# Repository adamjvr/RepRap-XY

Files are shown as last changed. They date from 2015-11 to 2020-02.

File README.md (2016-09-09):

# RepRap-XY-Iteration-2
## Open Source CoreXY RepRap 3D Printer
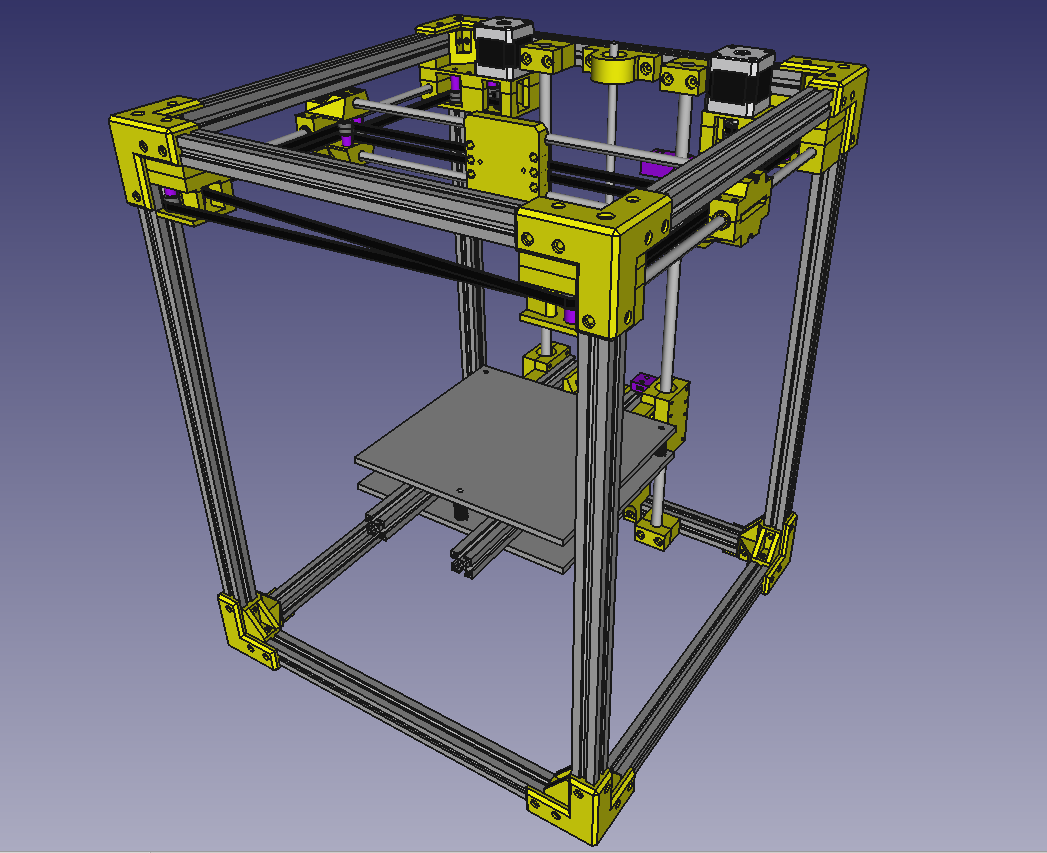
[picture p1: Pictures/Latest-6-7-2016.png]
RepRap-XY Iteration 2 Assembly

 RepRap-XY Iteration 2 FreeCAD Assembly

This is a modified release of the RepRap-XY 3D printer. It is based on the excellent design of Jand archive at:https://github.com/jand1122/RepRap-XY

Their designs/variants are discussed in the RepRap forum at:: http://forums.reprap.org/read.php?4,297740

RepRap-XY-Iteration 2 is designed to be an improvement over the original RepRap-XY design provided by Jand1122. Iteration 2 incorporated a modified X carriage and XY blocks from sdavi and incorporates 2020 coner brackets inspired by user ybm.

Iteration 2 Modifications:
- Sdavi's XY Blocks modified for 8x12x30 Brash Bushings
- Custom X Carriage based on Sdavi's design remodeled from scratch
- Mounting for E3D V6, E3D Chimera, E3D Cyclops
- Increased Z axis height of 100mm, printer height 500mm
- Corner bracket parts for frame in lieu of metal right angle t-slot brackets
- Spacer corner brackets for motor blocks and idler blocks, also add structur to frame
- (x2) B'Struder Direct Driver Extruder w/ MK8 Driver Gear setup for 1.75mm Filament
- Mounting for Ultimachine Archim 32 Bit 3D Printer Motherboard
- Runs TinyG motion control firmware on Ultimachine Archim for superior performance and resolution like no other

## Bill of Materials

Frame
- (4x) 500mm 20x20 Length of Aluminum Extrusion
- (12x) 260mm 20x20 Length of Aluminum Extrusion
- Lots of M4 T-nuts
- (24x) Printed Corner Brackets
- (4x) Printed Inner Corner Brackets

Z Axis
- (2x) 12mm Rod 500mm
- Trapizoidal Lead Screw
- 5X10 Motor Coupler
- (2x) LM12LUU 12mm Long Linear Bearing
- Nema17 Stepper Motor
- (4x) M4 T-nuts
- (2x) 100mm 20x20 Aluminum Extrustion Length
- 14x 40mm M5 bolt
- (8x) 25mm M5 bolt
- (4x) 15mm M3 bolt (to attach nema motor)

X & Y Axis
- (2x) NEMA17 Stepper Motors
- (24x) F624ZZ flanged bearings
- (2x) 330-350mm 8mm diameter smooth rod (y-axis)
- (2x) 400mm 8mm diameter smooth rod (x-axis)
- (6x) LM8UU 8mm linear bearing
- Approx. 3-4m GT2 belt
- (2x) 20 tooth GT2 Pulley
- (4x) 60mm M4 bolts (for XY block bearings)
- (40x) M4 bolts
- (12x) 40mm M3 bolts
- (8x) 40mm M4 bolts (for idler bearings, screws can be longer)
- (8x) 25mm M5 bolts
- (6x) 55mm M5 bolts
- (4x) 30mm M5 bolts
- (6x) 15mm M3 bolt
- (8x) 10mm M3 bolt (attach nema motors)

Release Notes:
- Stepper Motor Model Borrowed from:https://grabcad.com/library/nema-17-1
- Screws Borrowed from: https://github.com/FreeCAD/FreeCAD-library

Liscensing:
Creative Commons Attribution-ShareAlike 4.0 International License

https://creativecommons.org/licenses/by-sa/4.0/legalcode

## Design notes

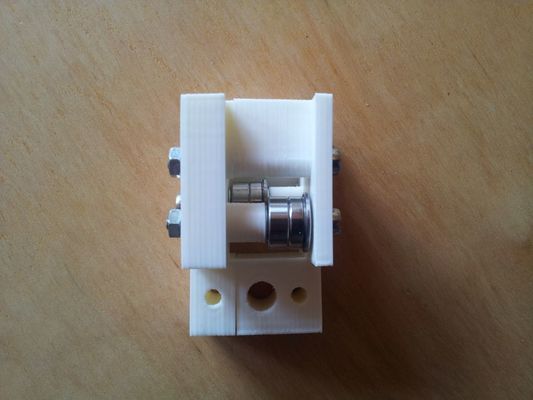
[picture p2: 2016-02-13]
Pictures/frontcorner.jpg

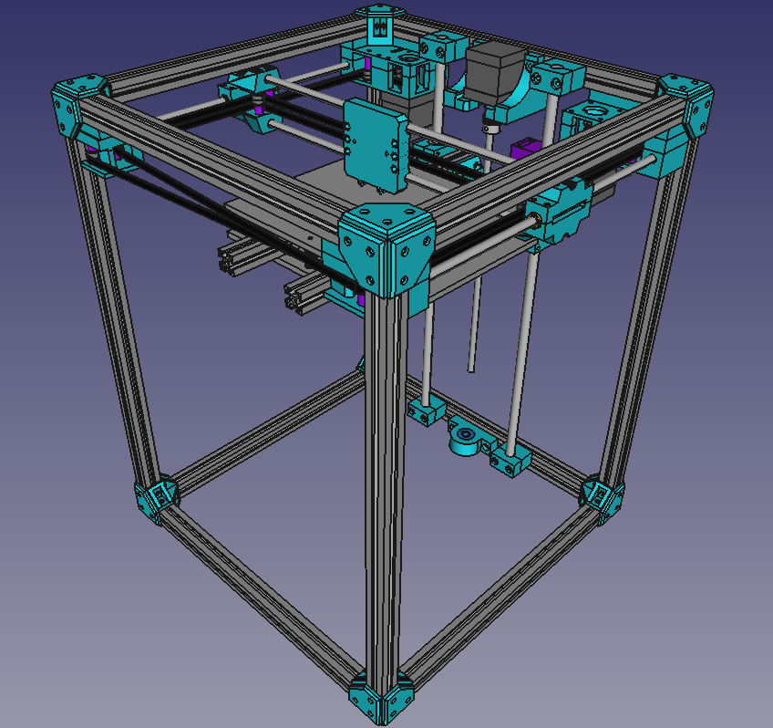
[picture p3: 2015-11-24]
Pictures/RepRapXYi2.png

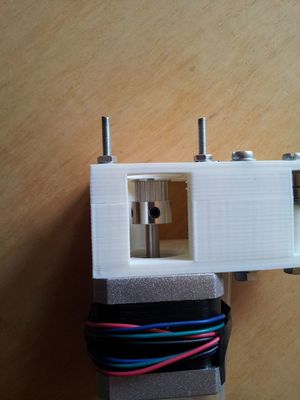
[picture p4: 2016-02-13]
Pictures/rightmotormount2.jpg

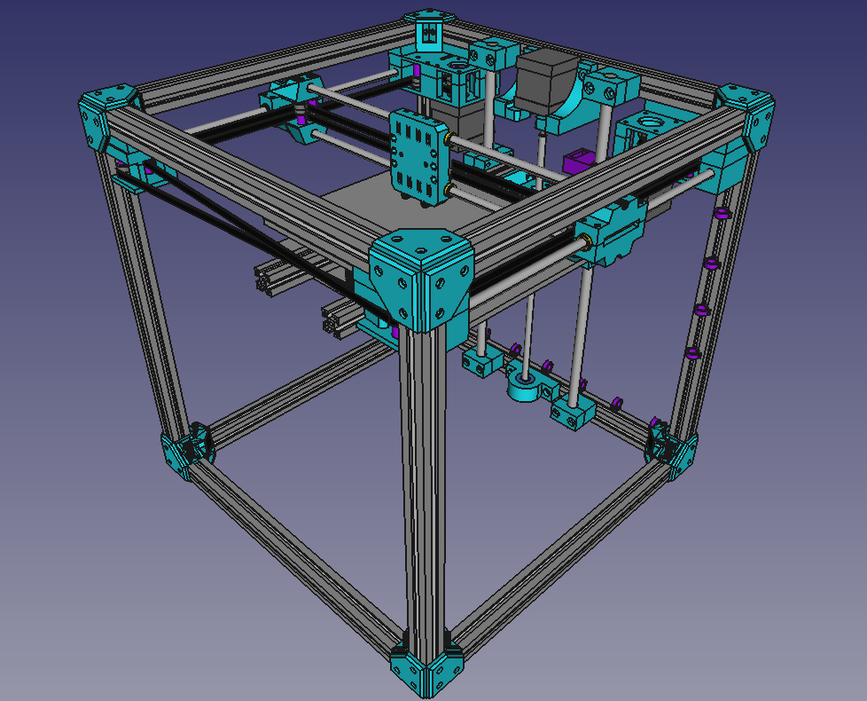
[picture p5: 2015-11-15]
Pictures/rxyi2.png

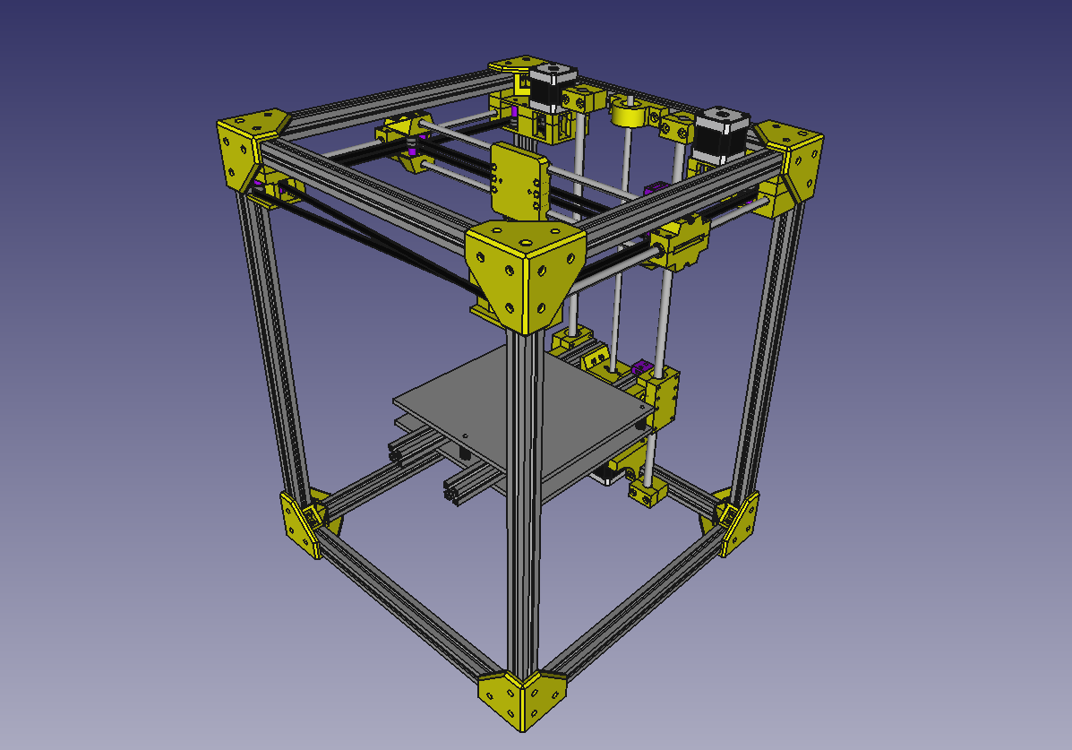
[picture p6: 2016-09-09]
Pictures/latest-rev-6-5-16.png

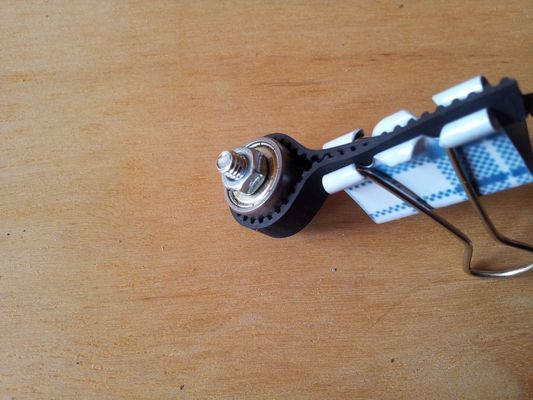
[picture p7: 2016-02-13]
Pictures/bearing3.jpg

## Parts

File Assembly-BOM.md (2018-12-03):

# RepRap-XY-Iteration-2
## Open Source CoreXY RepRap 3D Printer
### Assembly BOM

###### XY Axis Pulley-Motor-Box A
* 1x Printed Pulley-Motor-Box-A Top
* 1x Printed Pulley-Motor-Box-A Bottom
* 4x M3 40mm Hex Head Socket Cap screws
* 4x M3 Washers
* 3x M4 40mm Hex Head Socket Cap Screws
* 3x M4 Washers
* 3x Nylock Nuts
* 4x 9mm Printed Spacer
* 4x  F624Z Flanged bearings
* 1x NEMA17 Stepper Motor
* 1x 32 Tooth GT2 Pulley
* 1x Pulley Setscrew

###### XY Axis Pulley-Motor-Box B
* 1x Printed Pulley-Motor-Box-B Top
* 1x Printed Pulley-Motor-Box-B Bottom
* 4x M3 40mm Hex Head Socket Cap screws
* 4x M3 Washers
* 4x M4 40mm Hex Head Socket Cap Screws
* 7x M4 Washers
* 3x M4 Nylock Nuts
* 3x 16mm Printed Spacer
* 6x  F624Z Flanged bearings
* 1x NEMA17 Stepper Motor
* 1x 32 Tooth GT2 Pulley
* 1x Pulley Setscrew

###### XY Axis Bearing Idler Block A
* 1x Printed Axis Bearing Idler Block A Top
* 1x Printed Axis Bearing Idler Block A Bottom
* 4x M4 40mm Hex Head Socket Cap Screws
* 4x M4 Washers
* 4x  F624Z Flanged bearings
* 2x 9mm Spacers

###### XY Axis Bearing Idler Block B
* 1x Printed Axis Bearing Idler Block B Top
* 1x Printed Axis Bearing Idler Block B Bottom
* 4x M4 40mm Hex Head Socket Cap Screws
* 4x M4 Washers
* 4x  F624Z Flanged bearings
* 2x 9mm Spacers

###### XY Gantry
* 4x Printed XYBlocks
* 1x Printed Printhead Carriage
* 4x Printed Carriage GT2 Belt Clamps
* 1x Printed Hotend Mount
* 4x M4 70mm Hex Head Socket Cap Screws
* 8x F624 Flanged Bearings
* 8x M3 25mm Hex Head Socket Cap Screws
* 8x M3 Washer
* 8x M3 Nylock Nuts
* 4x Small Zip Ties
* 4x 30mm 8mm ID 12mm OD Brash Bushing With Graphite
* 4x 400mm 8mm Hardened Steel Precision Smooth Rod
* XY Axis Bearing Idler Block A Assembly
* XY Axis Bearing Idler Block B Assembly
* XY Axis Motor Box A Assembly
* XY Axis Motor Box B Assembly

###### Frame
* 4x 400mm 2020 Alu Extrusion
* 4x 500mm 2020 Alu Extrusion
* 20x 2020 Extrusion Right Angle Bracket
* 40x M4 10mm Hex Head Socket Cap Screws
* 40x M4 Washers

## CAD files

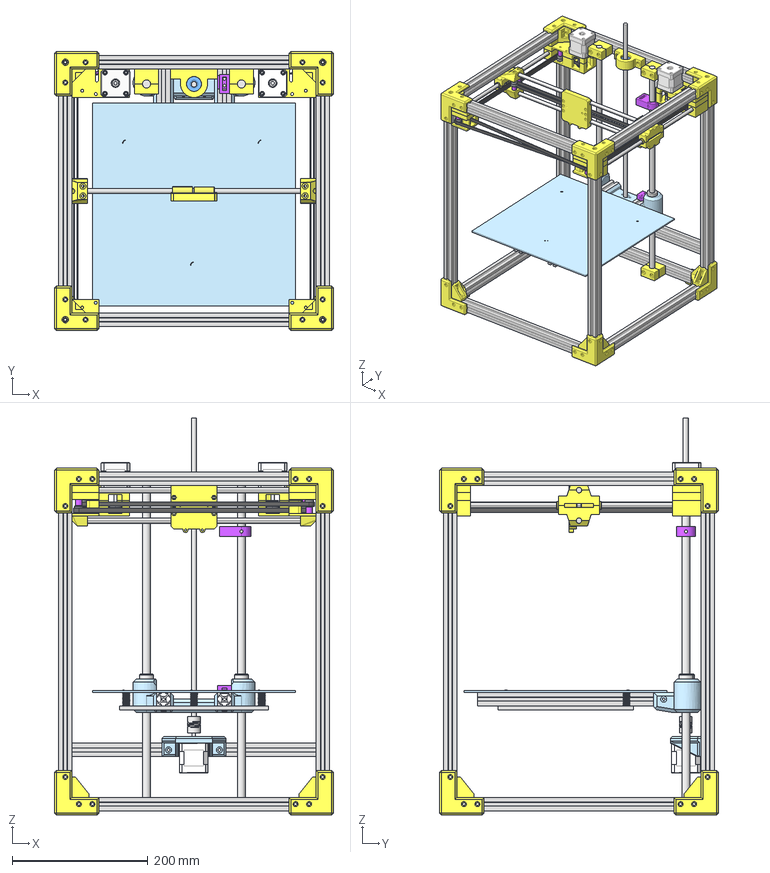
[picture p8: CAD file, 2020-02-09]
src/RepRap-XY-Iteration-2-Assembly.fcstd
412.0 x 412.0 x 586.0 mm
NEMA17-Z
NEMA17-AXES-2
NEMA17-AXES-1
Alu-20x20x501
Alu-20x20x505
Alu-20x20x506
Alu-20x20x507
Alu-20x20x360
Alu-20x20x361
Alu-20x20x362
Alu-20x20x363
Alu-20x20x367
Alu-20x20x368
Alu-20x20x369
Alu-20x20x370
XCarriage_Bushingmod_Step_AP214
XYBlock1_Bushing1
XYBlock1_Bushing2
XYBlock2_Bushing1
XYBlock2_Bushing2
CustomBushingXYBlockFromSTL
CustomBushingXYBlockFromSTL001
CustomBushingXYBlockFromSTL002
CustomBushingXYBlockFromSTL003
smooth-bar-8x330
smooth-bar-8x333
washer-M013
F624zz-bearing005
624-bearing005
spacer-002
washer-M014
washer-M015
F624zz-bearing006
624-bearing006
spacer-003
washer-M016
washer-M017
F624zz-bearing007
624-bearing007
spacer-004
washer-M018
washer-M019
F624zz-bearing
624-bearing
spacer-1
LM12LUU_1
LM12LUU_2
M8 Z Rod
Z-Axis-Rod-500mm
Z-Axis-Rod-500mm001
Coupler_5mm_to_8mm
BedMount
spring
spring001
spring002
Z-endstop-mount
Z-endstop-adjust
608-bearing
Z-leadscrew-bearing-block
Z-axis-clamp-2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

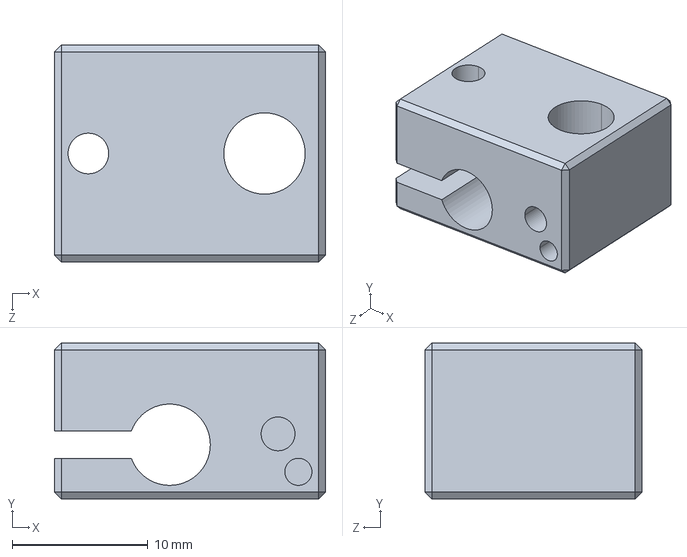
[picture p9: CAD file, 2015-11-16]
src/Hotends/Chimera STEP/heater block2.STEP
20.0 x 11.5 x 16.0 mm

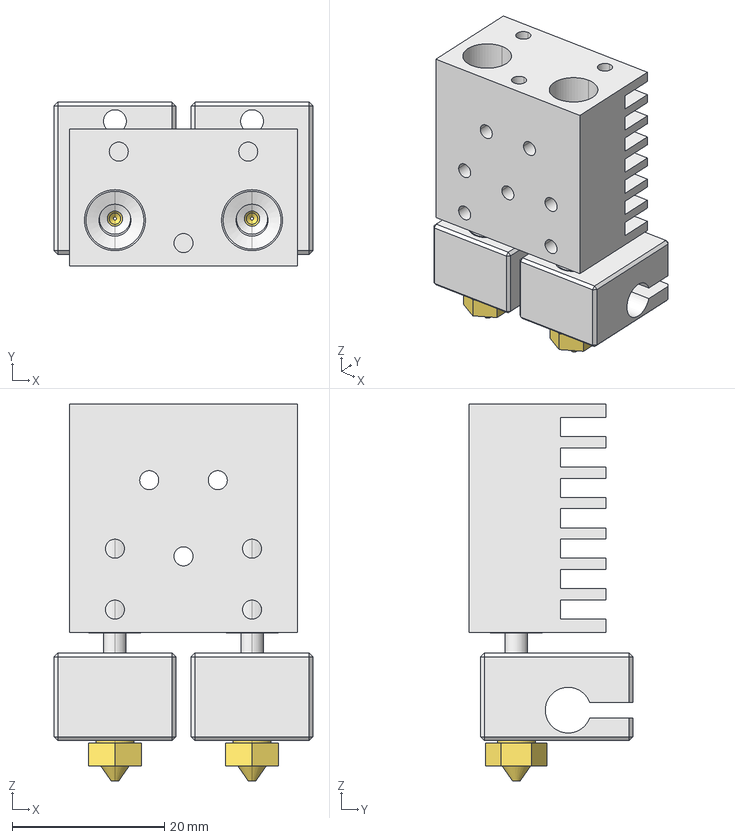
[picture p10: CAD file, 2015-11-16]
src/Hotends/Chimera.fcstd
34.0 x 21.5 x 49.5 mm
0.4 nozzle
heat break
heat sink
heater block
0.4 nozzle001
heat break001
heater block001

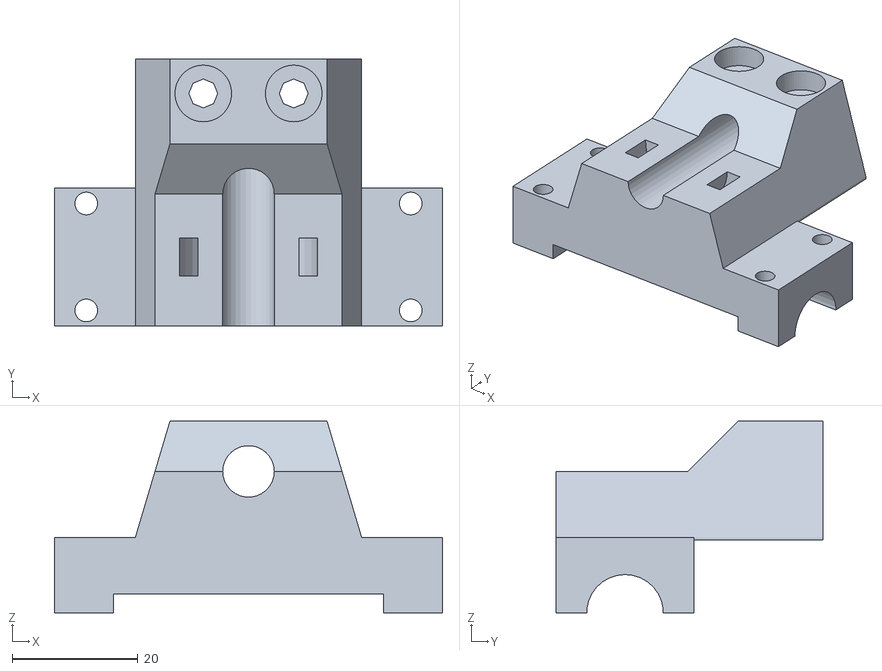
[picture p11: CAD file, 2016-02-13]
src/OpenSCAD src/xy_block_bushingmod.stl
61.7 x 42.5 x 30.5

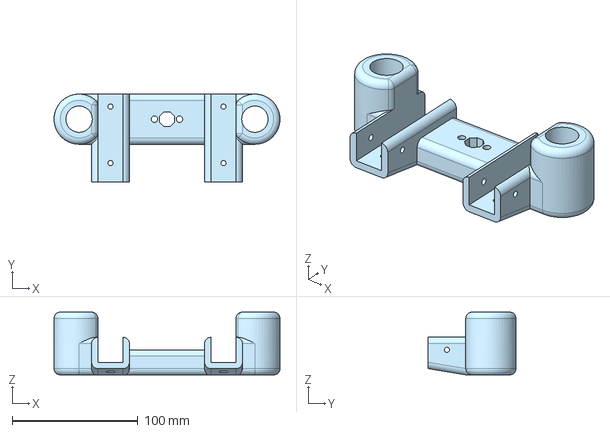
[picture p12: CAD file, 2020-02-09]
step/NewZ4Test.step
180.0 x 70.0 x 50.0 mm

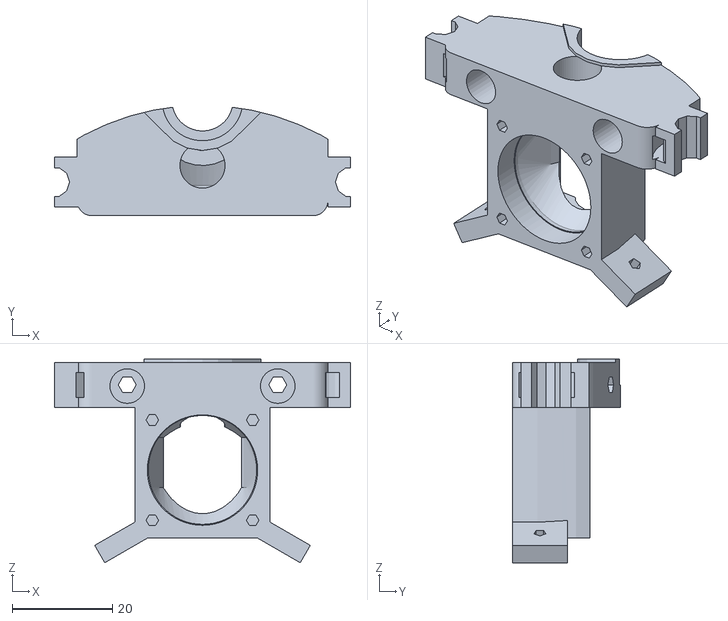
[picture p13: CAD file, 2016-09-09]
stl/jhead_bowden_mount_fan.stl
59.0 x 21.6 x 40.6

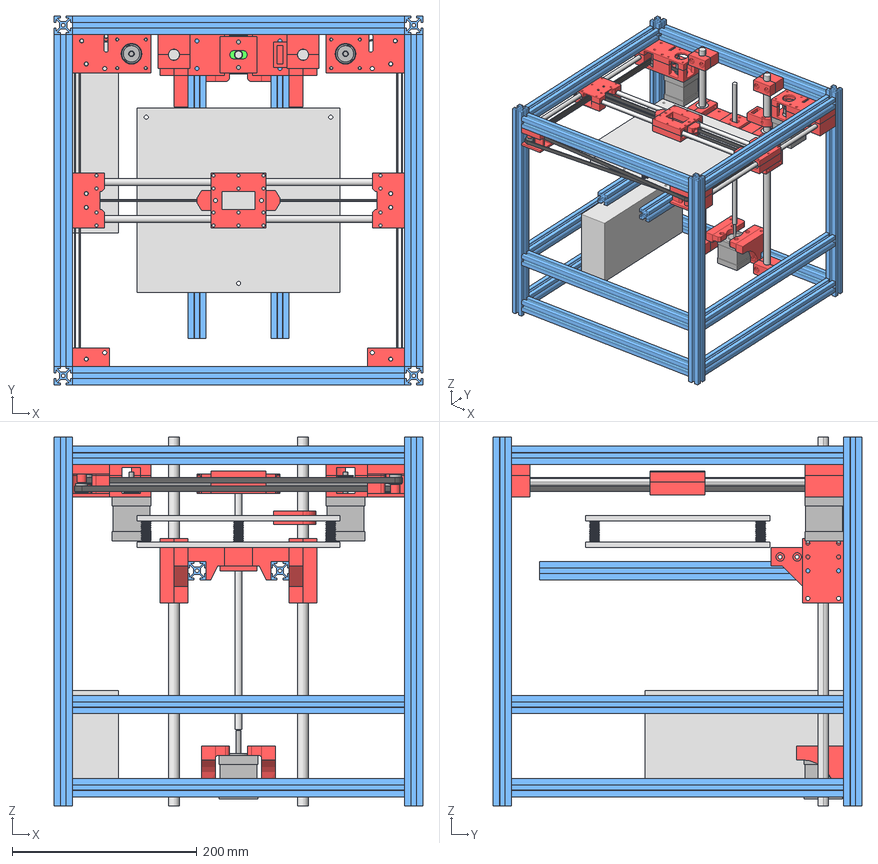
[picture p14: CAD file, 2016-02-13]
test/RepRap-XY-upsidedown-Z.FCStd
400.0 x 400.0 x 400.0 mm
Nema-17
Nema-018
Nema-019
Power_supply
F624zz-bearing
624-bearing
spacer-1
F624zz-bearing001
624-bearing001
washer-M4
washer-M005
F624zz-bearing002
624-bearing002
washer-M006
washer-M007
F624zz-bearing003
624-bearing003
washer-M008
washer-M009
F624zz-bearing004
624-bearing004
washer-M010
washer-M011
washer-M012
washer-M013
F624zz-bearing005
624-bearing005
spacer-002
washer-M014
washer-M015
F624zz-bearing006
624-bearing006
spacer-003
washer-M016
washer-M017
F624zz-bearing007
624-bearing007
spacer-004
washer-M018
washer-M019
F624zz-bearing008
624-bearing008
washer-M020
washer-M021
F624zz-bearing009
624-bearing009
washer-M022
washer-M023
F624zz-bearing010
624-bearing010
washer-M024
washer-M025
F624zz-bearing011
624-bearing011
washer-M026
washer-M027
smooth-bar-12x400
Alu-20x20x360
Alu-20x20x361
Alu-20x20x362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

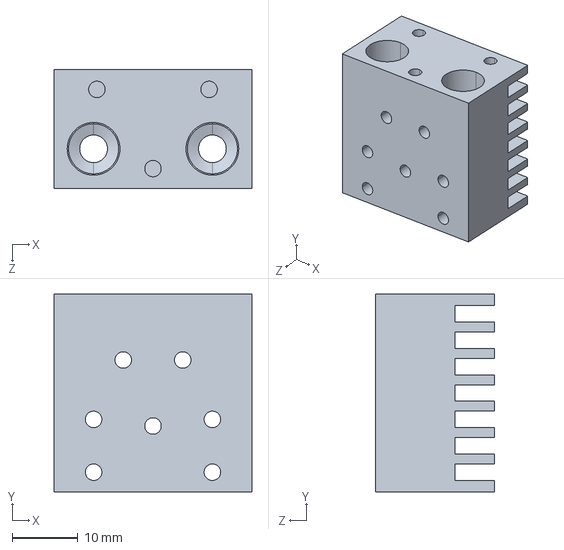
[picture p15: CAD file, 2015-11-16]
src/Hotends/Chimera STEP/heat sink.STEP
30.0 x 30.0 x 18.0 mm

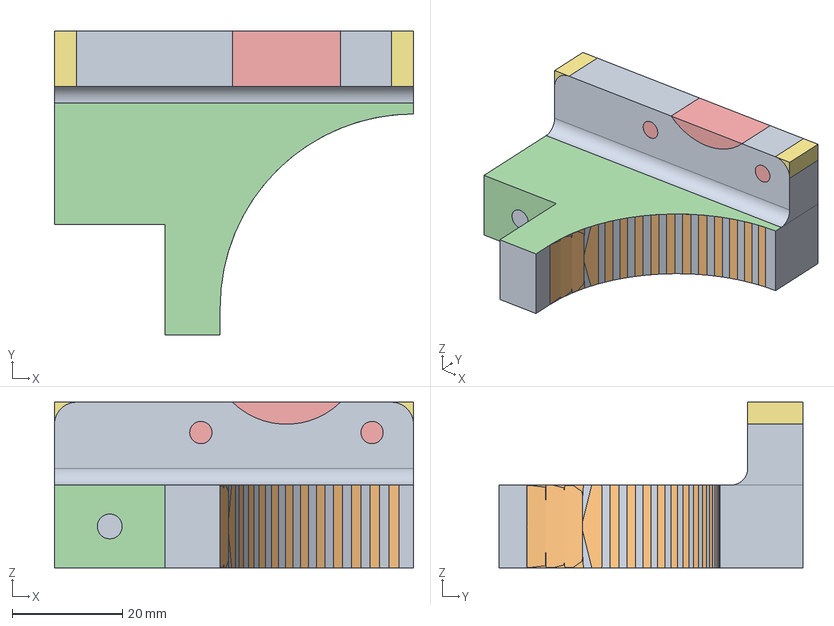
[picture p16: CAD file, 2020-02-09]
src/Z-motorMount.step
65.0 x 55.0 x 30.0 mm

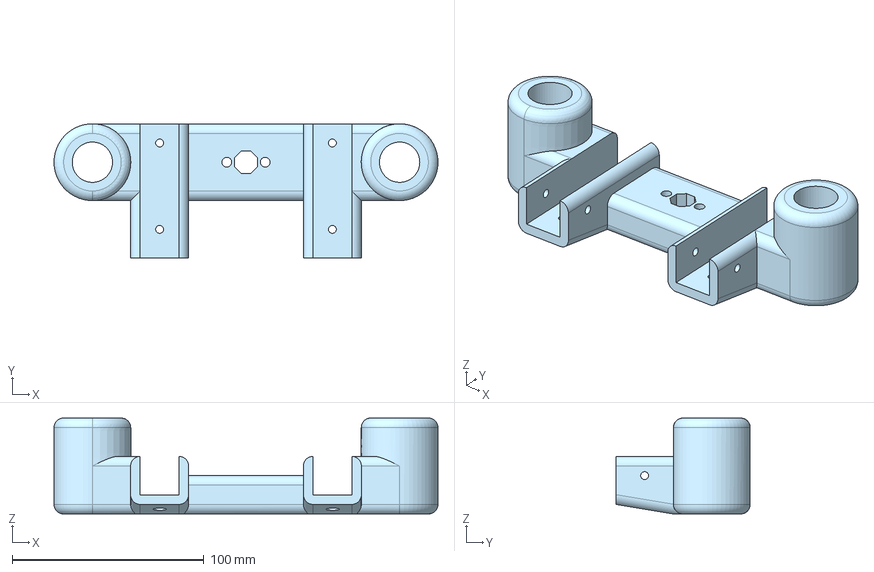
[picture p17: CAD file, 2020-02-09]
step/NewZStep.step
200.0 x 70.0 x 50.0 mm

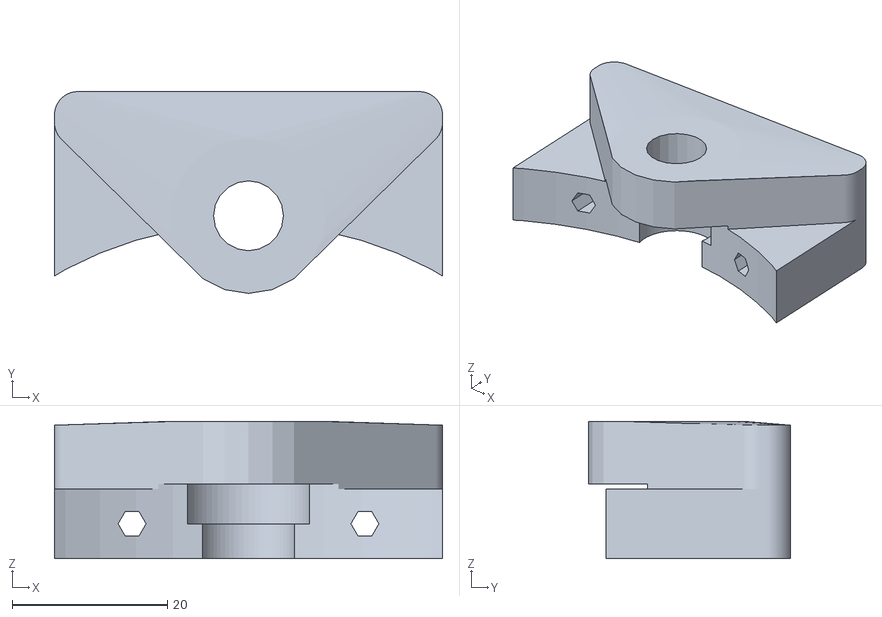
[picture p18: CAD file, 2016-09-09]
stl/jhead_bowden_mount.stl
50.0 x 26.0 x 17.7

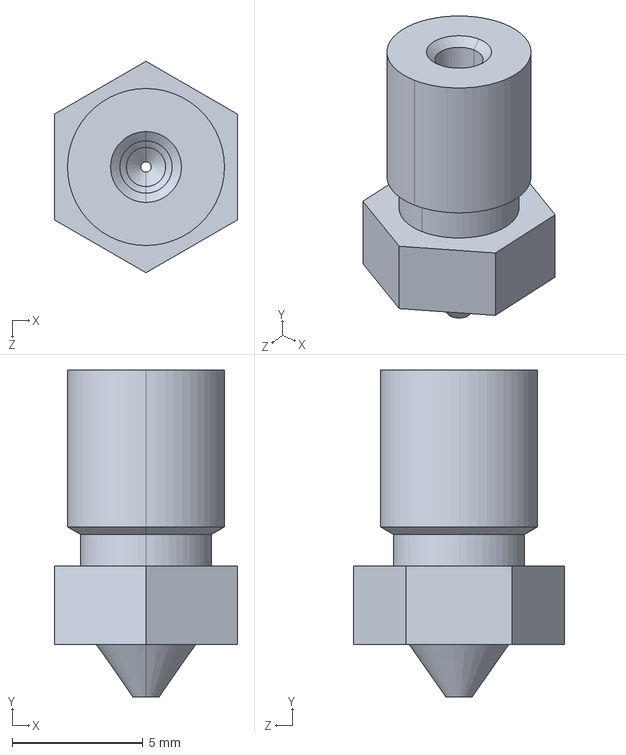
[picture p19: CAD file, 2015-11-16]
src/Hotends/Chimera STEP/0.4 nozzle.STEP
7.00 x 12.5 x 8.08 mm

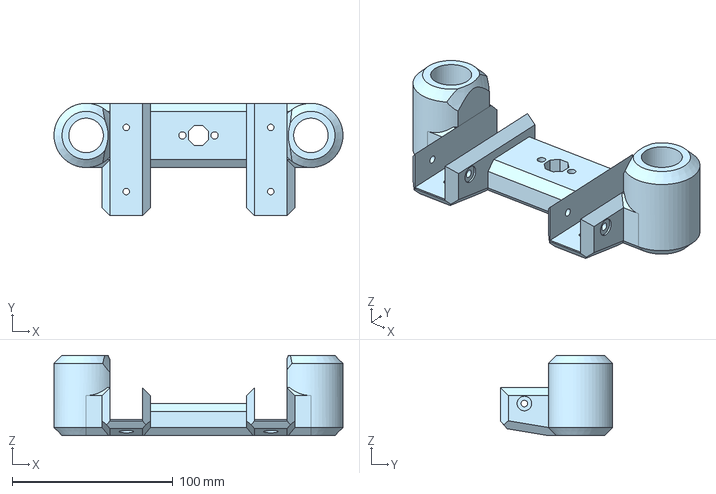
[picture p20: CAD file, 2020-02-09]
src/Z_STAGE.step
180.0 x 70.0 x 50.0 mm

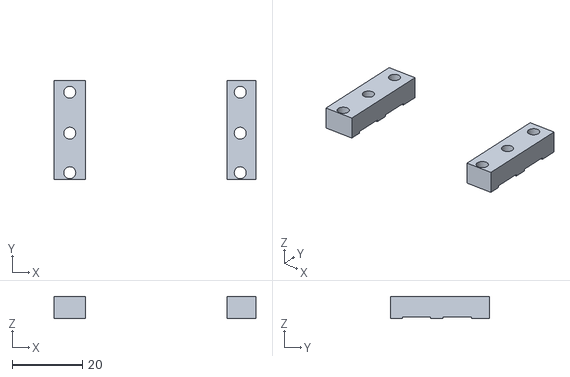
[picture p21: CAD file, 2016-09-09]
stl/x-carriage_belt_clamps.stl
57.5 x 28.2 x 6.34

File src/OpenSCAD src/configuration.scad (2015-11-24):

// Configuration
// Author: sdavi


include <dimensions.scad>
use <library.scad>


x_rod_distance = 45;

y_bearing = LM8UU;
y_bushing = BUSHING;
x_bearing = LM8UU;
x_bushing = BUSHING;
z_bearing = LM12LUU;
z_bushing = BUSHING;
belt_bearing = BEARING_2x624;


end_belt_bearing_distance = 25;// distance between 2 bearings on y-ends
belt_clearance = 9.5; //space for belts

frame_screw = M5; //m5 screws for v/tslot

frame_spacer_height = 18; //height to spacer to mount to frame to clear x-ends 


// calculated vars

//y bearing block
y_bearing_block_length = 2*y_bushing[2] + M3*2;
y_bearing_block_width = y_bearing[1]+5;
y_bearing_block_height = 6+y_bushing[1]/2;

xy_bearing_distance = y_bearing_block_width/2+belt_clearance+belt_bearing[1]/2; //distance between center of y-bearing to center of x-belt bearing 


//min height for belt bearings
min_beltbearing_height = max(((belt_bearing[2]+m4_washer_thickness*2) * 2), y_bearing_block_height);

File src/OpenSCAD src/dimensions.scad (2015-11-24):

// Dimensions
// Author: sdavi


BUSHING = [8, 12, 30]; //rod diameter,outer diameter, length
LM8UU = [8, 15, 24];
LM12UU = [12, 21, 30];
LM12LUU = [12, 21, 57];

BEARING_624 = [4,13,5]; //inner diameter(hole), outter diameter, thickness (http://reprap.org/wiki/Ball_bearing)
BEARING_2x624 = [4, 13, 10]; // 2 624 bearings together, good size for GT2

BEARING_6300 = [10,35,11]; //inner diameter, outer diameter, thickness


t_nut_length = 15+1; //hole in center 1mm cleanance incase hole isnt actually center


GT2_belt_width = 6;
GT2_belt_pitch = 2;
GT2_belt_thickness = 1.38;
GT2_belt_tooth_height = 0.75;  
GT2_belt_tooth_ratio = 0.5;



GT2_pulley_geared_diameter=12.2;//measured from top of tooth to top of tooth opp side// 12.2 is for the 20 tooth pulley

//from metric (prusa i3)
m4_diameter = 4.6;
m4_nut_diameter = 7.6;
m4_nut_diameter_horizontal = 8.15;

m3_diameter = 3.6;
m3_nut_diameter = 5.3;
m3_nut_diameter_horizontal = 6.8;
m3_washer_diameter = 6.9;
//end i3 variables

m5_diameter = 5.5;

//Hex Head M3x30: Head 5.5mm flat to flat, 2.12mm thick
m3_hex_head_diameter = 5.5*2/sqrt(3) + 0.2;

M4 = m4_diameter;
M3 = m3_diameter;
M5 = m5_diameter;
m4_washer_thickness = 0.8; //flat and penny washers
m4_washer_diameter = 9.6;

nema17_holes = 31;// mm between screws
nema17_width = 42; //width
nema17_height = 48;

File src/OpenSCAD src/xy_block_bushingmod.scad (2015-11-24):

// xy block  
// Author: sdavi


include <configuration.scad>
include <dimensions.scad>



use_xrod_clamp = true; //use ziptie clamps for xrod?
//clamp_ziptie = true;//use zipties to clamp rod

xy_block(top=1, clamp=use_xrod_clamp); //top
//translate([0,0,-5])mirror([0,0,1]) 
//xy_block(top=0, clamp=use_xrod_clamp); //bottom (nut trap for bearing end)

//clamp();



echo("Bearing Block Length: ", y_bearing_block_length);
echo("Bearing Block Width: ", y_bearing_block_width);
echo("Bearing Block Height: ", y_bearing_block_height);

wall_thickness = 2;


x_height = x_rod_distance+x_bearing[0] + wall_thickness*2+4;
x_width = x_bearing[0] * 2 + 20;//20 for some extra dist to screw down (todo what size?)
x_length = y_bearing_block_width/2+xy_bearing_distance+belt_bearing[1]/2;
x_top_width = GT2_belt_thickness+belt_bearing[1]+M4+6; 

module base(){
	union(){

		translate([2.75,-1,0]) 
            cube([y_bearing_block_length-5.5, y_bearing_block_width+2, y_bearing_block_height]); // bearing Block

            
        translate([0,-1,0])
            hull(){
            translate([y_bearing_block_length/2- GT2_belt_thickness/2 - belt_bearing[1]/2-M4/2-3, 0, x_height/2-1]) 
                cube([x_top_width, x_length, 1]);
            translate([y_bearing_block_length/2-x_width/2,0,0])
                cube([x_width, x_length, y_bearing_block_height]); //rod_block

            }
	}//end union

}





module clamp(){
	difference(){
		intersection(){
			base();
			x_rod_clamp();	
		}
		x_rod_screws();
		//cut hole for x_rod
		translate([y_bearing_block_length/2, x_length+0.1,x_rod_distance/2]) 
			rotate([90,0,0]) cylinder(d=x_bearing[0]+0.4, h=x_length+0.2, $fn=30);
	}
}




module xy_block(top=1, clamp=0){

	difference(){
		base();

		//cut to fit bearings for y_axis
		translate([(y_bearing_block_length-62)/2, y_bearing_block_width/2, 0])
			rotate([0,90,0])
				cylinder(d=y_bushing[1]+0.2, h=62+0.2, $fn=30);

		//cut middle to make easier to print top part without support
		translate([y_bearing_block_length/2-y_bearing[2]+5/2,-1.1,-.1])
			cube([y_bearing[2]*2-5, y_bearing_block_width+2.2, 3.1]);

		//cut hole for x_rod
		translate([y_bearing_block_length/2, x_length+.1,x_rod_distance/2]) 
			rotate([90,0,0]) 
                cylinder(d=x_bearing[0]+0.2, h=x_length+1.2, $fn=30);

		//clear X bearing area
		color("orange")translate([y_bearing_block_length/2-x_width/2-0.1,y_bearing_block_width,-.1])
			cube([x_width+0.2, x_length, min_beltbearing_height/2+.1]);
	
		//cut m4 screw hole to mount belt bearings
		for(x=[y_bearing_block_length/2- GT2_belt_thickness/2 - belt_bearing[1]/2,
			   y_bearing_block_length/2+ GT2_belt_thickness/2 + belt_bearing[1]/2]){
			
			translate([x, y_bearing_block_width/2+xy_bearing_distance,0]){
				cylinder(d=M4, h=x_height);
				//cut hole for head/nut
				if(top==1){
					translate([0, 0,x_height/2-4])
						cylinder(d=9, h=4.1, $fn=60);//3.4 min height for head
				} else {
					translate([0, 0,x_height/2-4])
						cylinder(d=m4_nut_diameter_horizontal, h=4, $fn=6);//3.4 min height for head
				}

			}
		}

		//screws for y bearing clamp (m3) (as jand next to bearings)
		translate([y_bearing_block_length/2, y_bearing_block_width/2, 0]){
			for(x=[-y_bearing[2]-M3/2, +y_bearing[2]+M3/2]){
				for(y=[y_bearing[0]/2+4.5, -y_bearing[0]/2-4.5]){
					translate([x,y,-.1])
                        cylinder(d=M3, h=x_height, $fn=60);
				}
			}
		}
		
		if(clamp==true){
			//make cutout for clamp and holes for screws
			translate([0,0,0]) x_rod_clamp();
			//if(clamp_ziptie==true){
				x_rod_ziptie();
			//} else {
				//x_rod_screws();
			//}
		}
	}//end difference
}



module x_rod_clamp(){

		//cut rod clamp for x-rod(with 45 deg slope so can print main piece without support)
		ch=(x_height-x_rod_distance)/2+.01;
		che = tan(45)*ch;

		
		translate([x_length+y_bearing_block_length/2-x_length/2,y_bearing_block_width,x_rod_distance/2])rotate([90,0,-90])linear_extrude(height=x_length, slices = 20)
			polygon( points=[[0,0],
				[y_bearing_block_width+1.1,0],
              	[y_bearing_block_width+1.1,ch],
				[-che,ch]] 
			);						
}

/*
module x_rod_screws(){

	//screws for x rod clamp (m3) 
	translate([y_bearing_block_length/2, y_bearing_block_width/2, 0]){

		for(x=[(-x_top_width/2-x_bearing[0]/2)/2, (x_top_width/2+x_bearing[0]/2)/2]){
			translate([x,0,0])cylinder(d=M3, h=x_height, $fn=60);
				
			//cut under for embedded screw
			//Hex Head M3x30: Head 5.5mm flat to flat, 2.12mm thick
			translate([x,0,0])cylinder(d=m3_hex_head_diameter, h=y_bearing[1]/2+3.3, $fn=6);

		}
	}
}
*/


module x_rod_ziptie(){

	translate([y_bearing_block_length/2, y_bearing_block_width/2, x_rod_distance/2])
		difference(){
			rotate([90,0,0])cylinder(d=x_bearing[0]+14, h=6, $fn=30, center=true);
			rotate([90,0,0])cylinder(d=x_bearing[0]+8, h=6, $fn=40, center=true);
		}
}

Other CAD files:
step/NewZSizeReduced.step
src/2020_NEMA17_VERT.step
src/Hotends/Chimera STEP/heat break2.STEP
step/Top2020FrameCorner.step
src/OpenSCAD src/library.scad
src/2020CornerPiece.fcstd
src/2020CornerPieceTrap.fcstd
src/2020TBracket.fcstd
src/Bottom2020FrameCorner.fcstd
src/BottomCornerBracket.fcstd
src/BrashBushing8x12x30.fcstd
src/BuildPlateATest.step
src/CornerSupport.fcstd
src/CustomBushingXYBlockFromSTL.fcstd
src/Hotends/Chimera STEP/heat break.STEP
src/InnerCornerSPRTFromSTL.fcstd
src/OpenBuilds8mmScrewNutePlateDelrin.fcstd
src/PS-mount.FCStd
src/RAMPS-mount-1.FCStd
src/RAMPS-mount-2.FCStd
src/RepRap-XY.FCStd
src/Screw M6x12 ISO4762 8,8 A2K.FCStd
src/Screws/Screw M3x10 ISO4762 8,8 A2K.FCStd
src/Screws/Screw M3x12 ISO4762 8,8 A2K.FCStd
src/Screws/Screw M3x30 ISO4762 8,8 A2K.FCStd
src/Screws/Screw M3x40 ISO4762 8,8 A2K.FCStd
src/Screws/Screw M4x10 ISO4762 8,8 A2K.FCStd
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

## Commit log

2015-11-13 sdavi parts added
    [CornerSupport.fcstd, CustomBushingXYBlockFromSTL.fcstd, CustomBushingXYBlockFromSTL.step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]
2015-11-13 corner mount brackets and plates modeled and applied within assembly
    [2020CornerPiece.fcstd, 2020CornerPieceTrap.fcstd, CornerSupportTrapizoid.step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]
2015-11-13 top corner brackets modeled and assembled
    [2020CornerPiece.fcstd, 2020LCorner.step, 2020LCorner10.step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]
2015-11-13 additional crossbeams added to top
    [2020TBracket.fcstd, TTrapBracked]t.fcstd]
2015-11-14 bushings modled and added, working on additional brackets, top brackets replaced with trapizoidal design
    [2020TBracket.fcstd, BrashBushing8x12x30.fcstd, BrassBushing8x12x30.step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]
2015-11-15 brackets switched, and spacers modeled in Onshape added
    [IdlerBlockSpacer.step, MotorBlockSpacer.step]
2015-11-15 spacers completed being modeled in Onshape, exported as STEP and imported into FreeCAD assembly, parts added and colored
    [2020LCorner.step, 2020LCorner10.step, 2020LCorner11.step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]
2015-11-16 new innnercorner brackets modeled in Onshape, imported and placed in assembly
    [0.4 nozzle.STEP, Chimera.fcstd, Part Studio 1 - InnerCornerBracket.step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]
2015-11-16 vertical 2020 extrusion pieces changed to 500mm, bottom frame adjusted, remodeled X-carriage by Will Frankian added.
    [0.4 nozzle2.STEP, 2020x500.step, 2020x500_2.step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]
2015-11-18 push for master approval
    [Coupler 5mm to 8mm.stp, Part Studio 1 - Z-Axis-Rod-500mm.step, Part Studio 1 - Z-Axis-Rod-500mm2.step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]
2015-11-19 updated modded X-carriage to have cutaway beneat zip tie guides for ease of assembly.
    [XCarriage_Bushingmod.IGS, XCarriage_Bushingmod.STL, XCarriage_Bushingmod_Step AP203.STEP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]
2015-11-23 LM12LUU bearings replacing LM12UU in the assembly
    [LM12LUU.step, LM12LUU_2.step, RepRap-XY-Iteration-2-Assembly.fcstd]
2015-11-24 added scad directory in src for easy access to modify the XY bearing scad file. spaced the bushings in the xy block and lengthened the y block properly for better fastener placement. first iteration 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
    [configuration.scad, dimensions.scad, library.scad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]
2015-11-24 widended xy block to make room for securing screws next to the bushing. cleaned up the code somewhat as well.
    [configuration.scad, xy_block_bushingmod.scad, xy_block_bushingmod.stl]
2015-12-28 Added new .stl files for trapezoids, brackets, and spacer blocks. Moved X Carriage and XY block stl files to the stl directory.
    [CornerSupportTrapezoid.stl, InnerCornerBracket.stl, Left Idler Block Spacer.stl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]
2016-01-11 New motor STEP added, motors flipped, Z motor moved to bottom, and new Z leadscrew added.
    [0.4 nozzle.STEP, 0.4 nozzle2.STEP, 2020CornerPiece.fcstd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]
2016-01-17 switching workstations
    [RepRap-XY-Iteration-2-Assembly.fcstd]
2016-01-18 Reorganized assembly CAD file, and added unfinished panels
    [Back-Panel-A.step, Screw M3x10 ISO4762 8,8 A2K.FCStd, Screw M3x10 ISO4762 8,8 A2K.step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]
2016-01-18 further cleanup, also in the last commit FreeCAD and STEP files for all screws were added
2016-02-08 - Screws added to frame (corner brackets) - Corner brackets modified for socket screw clearance, M6 screw holes for top and bottom brackets - Inner corner brackets modified to fit socket head screws 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
    [CornerSupportTrapizoid.step, CornerSupportTrapizoid10.step, CornerSupportTrapizoid11.step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]
2016-02-08 forgot to save assembly file, new push with saved progress.
    [RepRap-XY-Iteration-2-Assembly.fcstd]
2016-05-22 CAD files cleaned up and better organized
    [Part Studio 1 - LeftIdlerBlockSpacer.step, Part Studio 1 - LeftMotorBlockSpacer.step, Part Studio 1 - RightIdlerBlockSpacer.step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]
2016-05-23 Added new top and bottom corner brackets, bringing part cout down, new parts added to assembly
    [FrameCornerSupportBracket.step, FrameCornerSupportTopBottom.step, RepRap-XY-Iteration-2-Assembly.fcstd]
2016-06-02 Z axis core structure and nutrap completel redesigned and remodeled in OnShape, model added to assembly and freecad document created, same for ACME 8mm nut trap from open builds, Assembly is pending,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
    [RepRap-XY-Iteration-2-Assembly.fcstd, Z-nut-1.step, Z-nut-2.step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]
2016-06-02 New Zaxis core adjusted and replaced within assembly
    [RepRap-XY-Iteration-2-Assembly.fcstd]
2016-06-05 updated image
    [8mmACMENutPlate.step, BottomCornerBracket.fcstd, BottomCornerBracket.step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]
2016-06-09 New 2020 corner brackets and inner corner brackets, files cleaned up and made more current, still work in progress use at own risk
    [2020Corner.step, 2020InnerCorner.step, Bottom2020FrameCorner.fcstd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]
2018-12-03 Create Assembly-BOM.md
    Assembly bom
2020-02-09 CAD Update
    CAD assembly updated to relfect prototype, phase one. Next step is to flip motors and replace XY gantry with stock parts.
    [2020_NEMA17_VERT.step, BuildPlateATest.step, BuildPlateTestB.step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]
